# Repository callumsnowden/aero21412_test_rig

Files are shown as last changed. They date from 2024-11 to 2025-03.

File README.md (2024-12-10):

# aero21412_test_rig
AERO21412 Avionics Coursework 1 – Wind Tunnel Test Rig "Black Box"

## Description
A "black box" PCB that provides the interface between a number of sensors on the wind tunnel test rig and an external data acquisition system.The aim is to provide a number of outputs measuring supply voltage and current; motor torque, thrust and rotational speed. A PWM input signal should be provided that is passed directly to the ESC module.

## Signals to/from DAS
- [] RPM as voltage with scaling factor
- [] Scaled supply voltage
- [] Supply current as voltage with scaling factor
- [] UART for force measurements (optional control input)

## UART measurement packet specification

`<AAA,BB.BBB,CC.CCC>`

Measurements are transmitted at 20 Hz. The packet consists of a start character of `<` followed by an incrementing three-digit frame identifier `AAA`. After this follows a three decimal place measurement of thrust in Newtons `BB.BBB` and then a three decimal place measurement of torque in Newton metres `CC.CCC`. An end character `>` terminates the packet.

## Hardware

A Raspberry Pi Pico (RP2040) handles interfacing the load cells and photointerruptor and is responsible for transmitting UART messages plus generating an analogue voltage representing RPM.

### Sensors

- One load cell for thrust measurement (Siemens 7MH5102-1PD00) with a rated load of 5kg
- One load cell (analogue voltage output) for torque measurement (TE Connectivity FC2231-0000-0010-L) with a rated load of 10lbf (13.5 Nm) and a voltage output of 0.5-4.5V
- Photointerruptor for RPM measurement

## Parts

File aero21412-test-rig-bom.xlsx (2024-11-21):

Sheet: Electrical
AERO21412 Test Rig BOM
Rig build qty: | 1
Part | Manufacturer | Manufac. Part No. | Quantity Per Rig | Quantity to order total
1uF 0603 Cap | Samsung Electro-Mechanics | CL10A105KA8NNNC | 8 | 8
0.1uF 0603 Cap | Kemet | C0603C104Z3VAC7411 | 7 | 7
10uF 0603 Cap | Samsung Electro-Mechanics | CL10A106MP8NNNC | 2 | 2
22uF elec. Cap | Kemet | A768EB226M1HLAE048 | 1 | 1
47uF elec. Cap | Kemet | A768EB476M1VLAE042 | 1 | 1
SMAJ5.0A/TR13 | Yageo | SMAJ5.0A/TR13 | 4 | 4
CDSOT23-T05C | Bourns | CDSOT23-T05C | 3 | 3
Green LED | AMS Osram | KT EELP41.12-S2U1-25-2X4X-5-R18 | 1 | 1
4 pin WTB header | Molex | 22-27-2041 | 3 | 3
DB15 female conn. | Multicomp Pro | 5504F1-15S-02-03-F1 | 1 | 1
XT60-M connector | Amass | XT60-M | 1 | 1
XT60-F connector | Amass | XT60-F | 1 | 1
Molex connector | Molex | 22-27-2031 | 1 | 1
1x3 pin header | Multicomp Pro | 2211S-03G | 1 | 1
2x5 pin header | Multicomp Pro | 2213S-10G | 1 | 1
3.3uH ferrite | Wurth Elektronik | 742792656 | 1 | 1
MMBT4403 | Onsemi | MMBT4403LT1G | 1 | 1
2N7002BK,215 | Diodes Inc. | 2N7002BK,215 | 1 | 1
NX3008PBK,215 | Nexperia | NX3008PBK,215 | 1 | 1
100R 0603 resistor | Vishay | RCA0603100RFKEA | 2 | 2
3.3K 0603 resistor | Yageo | RC0603FR-133K3L | 6 | 6
20K 0603 resistor | Yageo | RC0603FR-1320KL | 2 | 2
8.2K 0603 resistor | Yageo | RC0603JR-078K2L | 1 | 1
110R 0805 resistor | Yageo | RC0805FR-07110RL | 1 | 1
1.6K 0603 resistor | Yageo | RC0603FR-071K6L | 1 | 1
5.1K 0603 resistor | Yageo | AC0603FR-135K1L | 1 | 1
9.76K 0603 resistor | Panasonic | ERJ3EKF9761V | 1 | 1
10K 0603 resistor | KOA | RK73B1JTTD103J | 1 | 1
2K 0603 resistor | KOA | RK73H1JTTD2001F | 1 | 1
1K 0603 resistor | KOA | RK73H1JTTD1001F | 4 | 4
Push button | TE Connectivity | FSM4JH | 1 | 1
Microcontroller | Raspberry Pi | RASPBERRY PI PICO | 1 | 1
ADS1100 | Texas Instruments | ADS1100A3IDBVT | 1 | 1
TXU0202DCUR | Texas Instruments | TXU0202DCUR | 1 | 1
LMV321 | Texas Instruments | LMV321IDBVR | 2 | 2
Current sensor | Allegro Microsystems | ACS724LLCTR-50AB-S | 1 | 1
5V PSU | XP Power | TR05S05 | 1 | 1
Photo interruptor | TT Electronics | OPB743WZ | 1 | 1
Strain gauge | Siemens | 7MH5102-1PD00 | 1 | 1
Load cell | TE Connectivity | FC2231-0000-0010-L | 1 | 1

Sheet: Mechanical
AERO21412 Test Rig BOM
Rig build qty: | 1
Part | Manufacturer | Manufac. Part No. | Quantity Per Rig | Quantity to order total
Plain bearing | Igus | GFL-10 | 2 | 2
10mm ID Shaft collar | RS Pro | 823-6954 | 2 | 2

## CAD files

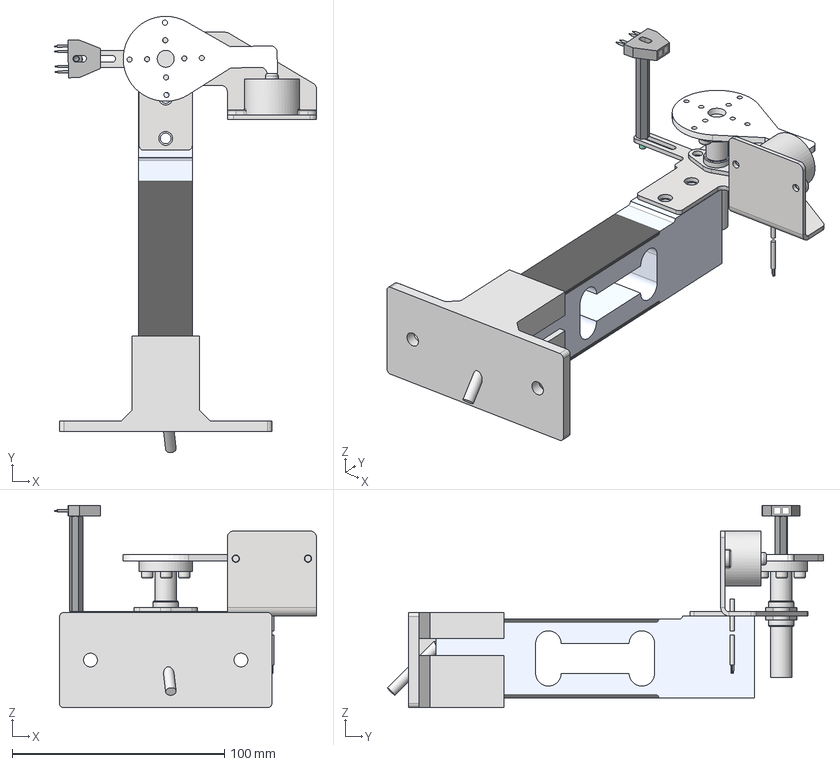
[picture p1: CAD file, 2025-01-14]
mechanical/MainAssembly.stp
123.4 x 205.4 x 95.2 mm
MotorMountPlate
MotorPlateSpindle
TorqueSensorMountPlate
ibh_GFL-10_2024102_1050_model x 2
c-fc2231-0000-0010-l-d-3d
7MH5102-1PD00_G_WT01_XX_00448V
ISO 4762 - M3 x 8 x 4
BaseStand
OPB742WZ
Download_STEP_971450321 (rev1)

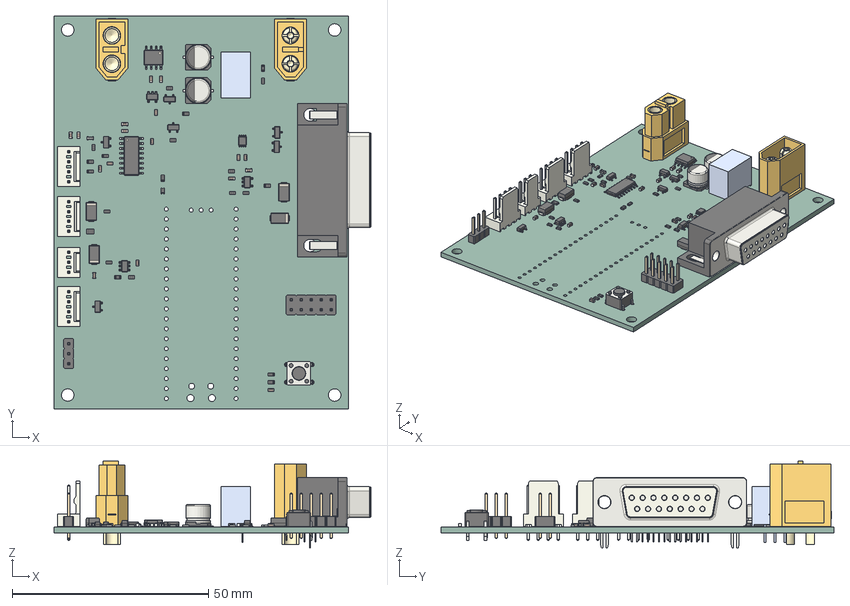
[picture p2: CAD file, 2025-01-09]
test-rig-black-box/test-rig-black-box.step
80.8 x 100.0 x 22.1 mm
SOT_23 x 6
C_0603_1608Metric x 17
R_0603_1608Metric x 20
DSUB_43_female
TR05
D_SMA x 4
VSSOP_8_23x2mm_P05mm
SOIC_8_39x49mm_P127mm
Molex_AE_6410_04A x 3
XT60 male v9
XT60 female v5
PinHeader_2x05_P254mm_Vertical
CP_Elec_63x57 x 2
D_0603
Molex_AE_6410_03A
R_0805_2012Metric
L_0603_1608Metric
SOT_23_5 x 2
SOT_23_6
SW_PUSH_6mm
SOP-16_3.9x9.9mm_P1.27mm
PinHeader_1x03_P254mm_Vertical
test-rig-black-box_PCB

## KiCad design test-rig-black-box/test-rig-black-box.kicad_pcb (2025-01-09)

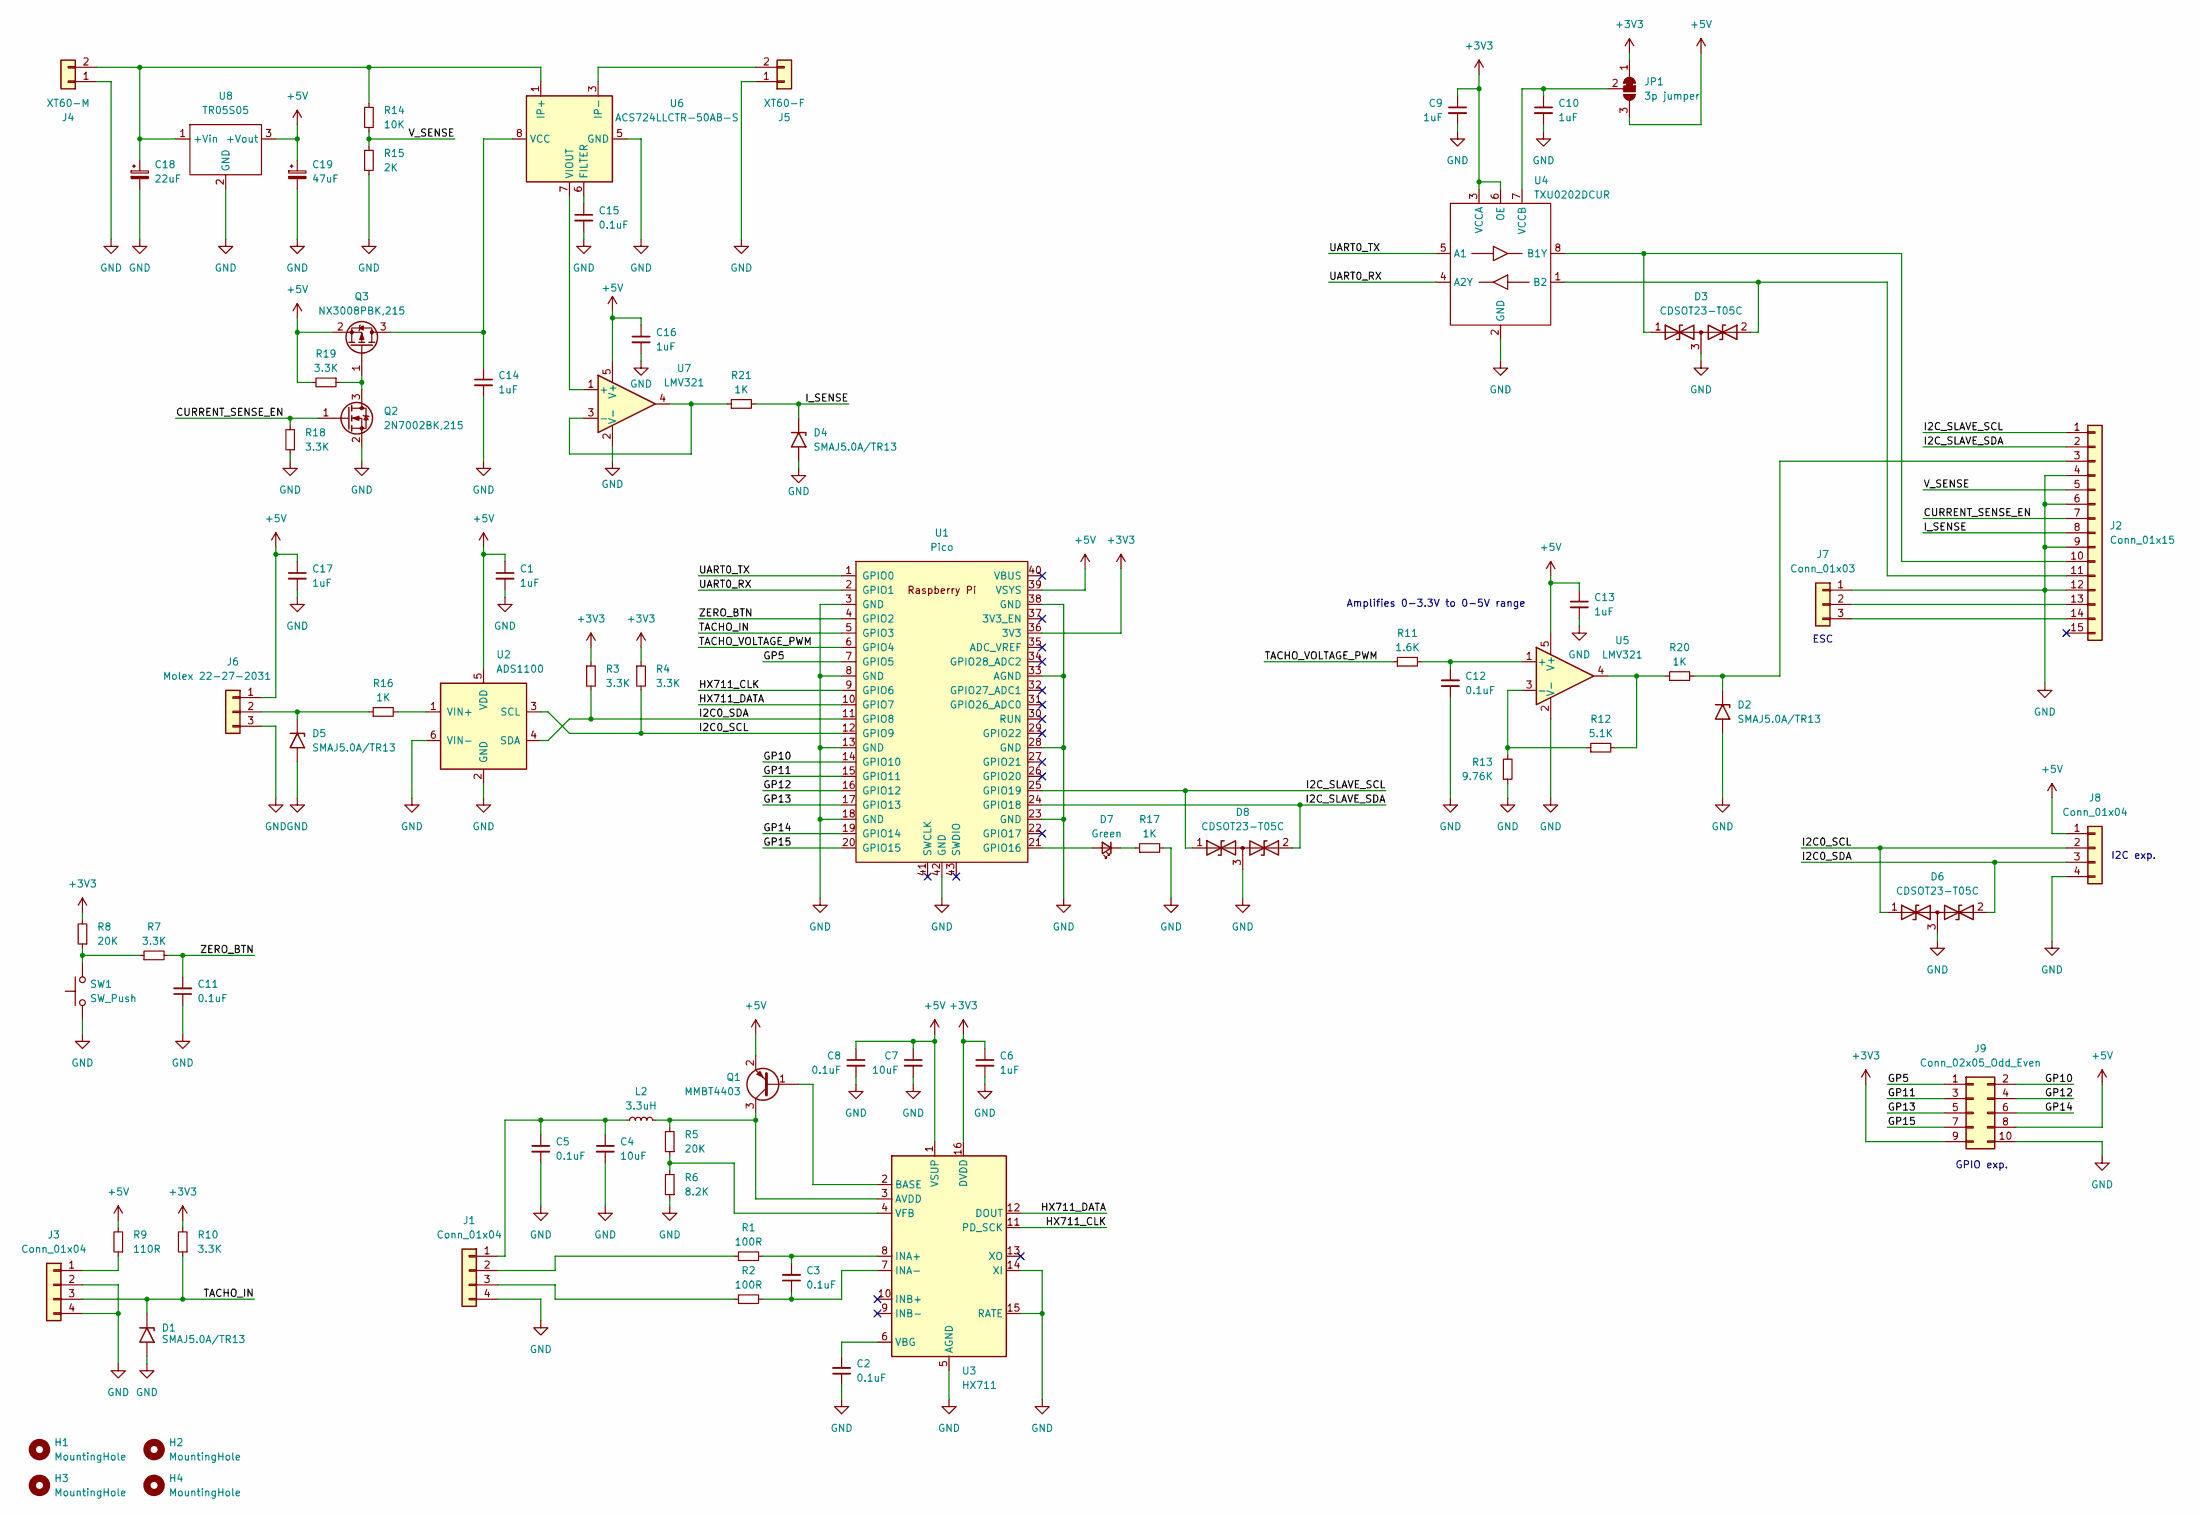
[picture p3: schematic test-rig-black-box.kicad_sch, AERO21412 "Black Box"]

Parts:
C1, C6, C9, C10, C13, C14, C16, C17: 1uF; C_0603_1608Metric; ManufacturerPartNumber CL10A105KA8NNNC
C2, C3, C5, C8, C11, C12, C15: 0.1uF; C_0603_1608Metric; ManufacturerPartNumber C0603C104Z3VAC7411
C4, C7: 10uF; C_0603_1608Metric; ManufacturerPartNumber CL10A106MP8NNNC
C18: 22uF; CP_Elec_6.3x5.7; ManufacturerPartNumber A768EB226M1HLAE048
C19: 47uF; CP_Elec_6.3x5.7; ManufacturerPartNumber A768EB476M1VLAE042
D1, D2, D4, D5: SMAJ5.0A/TR13; D_SMA; ManufacturerPartNumber SMAJ5.0A/TR13
D3, D6, D8: CDSOT23-T05C; SOT-23; ManufacturerPartNumber CDSOT23-T05C
D7: Green; D_0603_1608Metric; ManufacturerPartNumber KT EELP41.12-S2U1-25-2X4X-5-R18
H1, H2, H3, H4: MountingHole; MountingHole_3.2mm_M3
J1, J3, J8: Conn_01x04; Molex_KK-254_AE-6410-04A_1x04_P2.54mm_Vertical; ManufacturerPartNumber 22-27-2041
J2: Conn_01x15; DSUB-15_Female_Horizontal_P2.77x2.84mm_EdgePinOffset7.70mm_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; ManufacturerPartNumber 5504F1-15S-02-03-F1
J4: XT60-M; AMASS_XT60-M_1x02_P7.20mm_Vertical; ManufacturerPartNumber XT60-M
J5: XT60-F; AMASS_XT60-F_1x02_P7.20mm_Vertical; ManufacturerPartNumber XT60-F
J6: Molex 22-27-2031; Molex_KK-254_AE-6410-03A_1x03_P2.54mm_Vertical; ManufacturerPartNumber 22-27-2031
J7: Conn_01x03; PinHeader_1x03_P2.54mm_Vertical; ManufacturerPartNumber 2211S-03G
J9: Conn_02x05_Odd_Even; PinHeader_2x05_P2.54mm_Vertical; ManufacturerPartNumber 2213S-10G
JP1: 3p jumper; SolderJumper-3_P1.3mm_Bridged12_RoundedPad1.0x1.5mm_NumberL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
L2: 3.3uH; L_0603_1608Metric; ManufacturerPartNumber 742792656
Q1: MMBT4403; SOT-23; ManufacturerPartNumber MMBT4403LT1G
Q2: 2N7002BK,215; SOT-23; ManufacturerPartNumber 2N7002BK,215
Q3: NX3008PBK,215; SOT-23; ManufacturerPartNumber NX3008PBK,215
R1, R2: 100R; R_0603_1608Metric; ManufacturerPartNumber RCA0603100RFKEA
R3, R4, R7, R10, R18, R19: 3.3K; R_0603_1608Metric; ManufacturerPartNumber RC0603FR-133K3L
R5, R8: 20K; R_0603_1608Metric; ManufacturerPartNumber RC0603FR-1320KL
R6: 8.2K; R_0603_1608Metric; ManufacturerPartNumber RC0603JR-078K2L
R9: 110R; R_0805_2012Metric; ManufacturerPartNumber RC0805FR-07110RL
R11: 1.6K; R_0603_1608Metric; ManufacturerPartNumber RC0603FR-071K6L
R12: 5.1K; R_0603_1608Metric; ManufacturerPartNumber AC0603FR-135K1L
R13: 9.76K; R_0603_1608Metric; ManufacturerPartNumber ERJ3EKF9761V
R14: 10K; R_0603_1608Metric; ManufacturerPartNumber RK73B1JTTD103J
R15: 2K; R_0603_1608Metric; ManufacturerPartNumber RK73H1JTTD2001F
R16, R17, R20, R21: 1K; R_0603_1608Metric; ManufacturerPartNumber RK73H1JTTD1001F
SW1: SW_Push; SW_PUSH_6mm; ManufacturerPartNumber FSM4JH
U1: Pico; RPi_Pico_SMD_TH; ManufacturerPartNumber Pico
U2: ADS1100; SOT-23-6; ManufacturerPartNumber ADS1100A3IDBVT
U3: HX711; SOP-16_3.9x9.9mm_P1.27mm; ManufacturerPartNumber HX711
U4: TXU0202DCUR; VSSOP-8_2.3x2mm_P0.5mm; ManufacturerPartNumber TXU0202DCUR
U5, U7: LMV321; SOT-23-5; ManufacturerPartNumber LMV321IDBVR
U6: ACS724LLCTR-50AB-S; SOIC-8_3.9x4.9mm_P1.27mm; ManufacturerPartNumber ACS724LLCTR-50AB-S
U8: TR05S05; TR05Sxx; ManufacturerPartNumber TR05S05

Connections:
+3V3: C6.1, C9.1, J9.9, JP1.1 (A), R3.1, R4.1, R8.2, R10.2, U1.36 (3V3), U3.16 (DVDD), U4.3 (VCCA), U4.6 (OE)
+5V: C1.1, C7.1, C8.1, C13.1, C16.1, C17.1, C19.1, J6.1, J8.1, J9.8, JP1.3 (B), Q1.2 (E), Q3.2 (S), R9.2, R19.2, U1.39 (VSYS), U2.5 (VDD), U3.1 (VSUP), U5.5 (V+), U7.5 (V+), U8.3 (+Vout)
/CURRENT_SENSE_EN: J2.7, Q2.1 (G), R18.2
/GP5: J9.1, U1.7 (GPIO5)
/GP10: J9.2, U1.14 (GPIO10)
/GP11: J9.3, U1.15 (GPIO11)
/GP12: J9.4, U1.16 (GPIO12)
/GP13: J9.5, U1.17 (GPIO13)
/GP14: J9.6, U1.19 (GPIO14)
/GP15: J9.7, U1.20 (GPIO15)
/HX711_CLK: U1.9 (GPIO6), U3.11 (PD_SCK)
/HX711_DATA: U1.10 (GPIO7), U3.12 (DOUT)
/I2C0_SCL: D6.1 (A1), J8.2, R4.2, U1.12 (GPIO9), U2.3 (SCL)
/I2C0_SDA: D6.2 (A2), J8.3, R3.2, U1.11 (GPIO8), U2.4 (SDA)
/I2C_SLAVE_SCL: D8.1 (A1), J2.1, U1.25 (GPIO19)
/I2C_SLAVE_SDA: D8.2 (A2), J2.2, U1.24 (GPIO18)
/I_SENSE: D4.1 (A1), J2.8, R21.2
/TACHO_IN: D1.1 (A1), J3.3, R10.1, U1.5 (GPIO3)
/TACHO_VOLTAGE_PWM: R11.1, U1.6 (GPIO4)
/UART0_RX: U1.2 (GPIO1), U4.4 (A2Y)
/UART0_TX: U1.1 (GPIO0), U4.5 (A1)
/V_SENSE: J2.5, R14.2, R15.1
/ZERO_BTN: C11.2, R7.2, U1.4 (GPIO2)
GND: C1.2, C2.1, C4.2, C5.2, C6.2, C7.2, C8.2, C9.2, C10.2, C11.1, C12.1, C13.2, C14.2, C15.2, C16.2, C17.2, C18.2, C19.2, D1.2 (A2), D2.2 (A2), D3.3 (common), D4.2 (A2), D5.2 (A2), D6.3 (common), D8.3 (common), J1.4, J2.4, J2.6, J2.9, J2.12, J3.2, J3.4, J4.1, J5.1, J6.3, J7.1, J8.4, J9.10, Q2.2 (S), R6.1, R13.1, R15.2, R17.2, R18.1, SW1.1, U1.3 (GND), U1.8 (GND), U1.13 (GND), U1.18 (GND), U1.23 (GND), U1.28 (GND), U1.33 (AGND), U1.38 (GND), U1.42 (GND), U2.2 (GND), U2.6 (VIN-), U3.5 (AGND), U3.14 (XI), U3.15 (RATE), U4.2 (GND), U5.2 (V-), U6.5 (GND), U7.2 (V-), U8.2 (GND)
unnamed: D2.1 (A1), J2.3, R20.2
unnamed: D3.1 (A1), J2.10, U4.8 (B1Y)
unnamed: D3.2 (A2), J2.11, U4.1 (B2)
unnamed: D5.1 (A1), J6.2, R16.1
unnamed: D7.2 (A), U1.21 (GPIO16)
unnamed: D7.1 (K), R17.1
unnamed: C4.1, C5.1, J1.1, L2.1
unnamed: J1.2, R1.1
unnamed: J1.3, R2.1
unnamed: J2.13, J7.2
unnamed: J2.14, J7.3
unnamed: J3.1, R9.1
unnamed: C18.1, J4.2, R14.1, U6.1 (IP+), U6.2 (IP+), U8.1 (+Vin)
unnamed: J5.2, U6.3 (IP-), U6.4 (IP-)
unnamed: C10.1, JP1.2 (C), U4.7 (VCCB)
unnamed: Q1.1 (B), U3.2 (BASE)
unnamed: L2.2, Q1.3 (C), R5.2, U3.3 (AVDD)
unnamed: Q2.3 (D), Q3.1 (G), R19.1
unnamed: C14.1, Q3.3 (D), U6.8 (VCC)
unnamed: R7.1, R8.1, SW1.2
unnamed: R12.2, R20.1, U5.4
unnamed: R16.2, U2.1 (VIN+)
unnamed: C3.2, R1.2, U3.8 (INA+)
unnamed: C3.1, R2.2, U3.7 (INA-)
unnamed: C2.2, U3.6 (VBG)
unnamed: R5.1, R6.2, U3.4 (VFB)
unnamed: C12.2, R11.2, U5.1 (+)
unnamed: R12.1, R13.2, U5.3 (-)
unnamed: C15.1, U6.6 (FILTER)
unnamed: U6.7 (VIOUT), U7.1 (+)
unnamed: R21.1, U7.3 (-), U7.4

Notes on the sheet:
GPIO exp.
Amplifies 0-3.3V to 0-5V range
ESC
I2C exp.

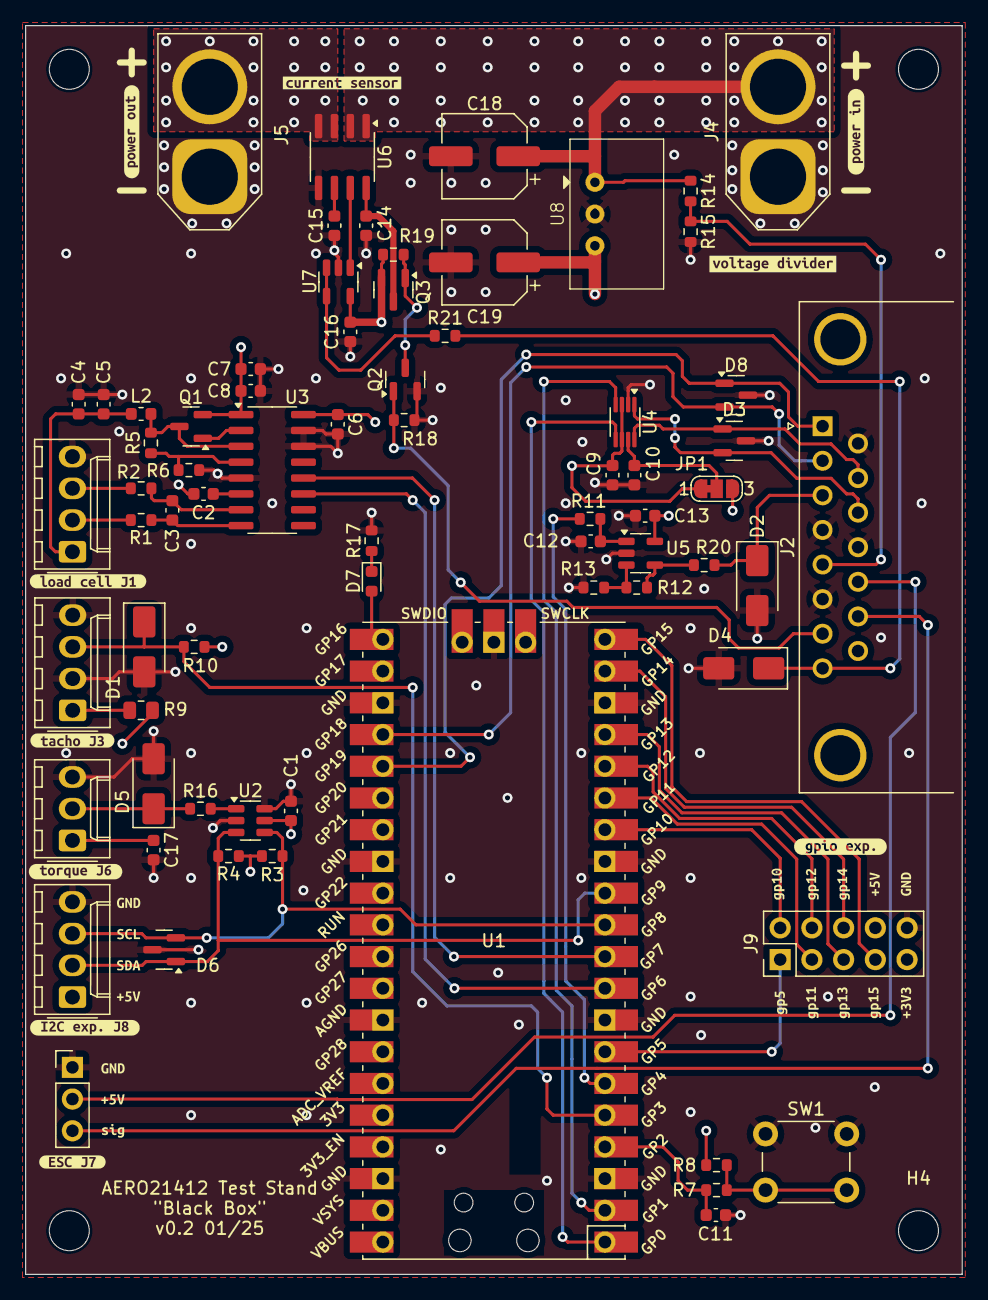
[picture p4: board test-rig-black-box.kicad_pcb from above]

Board: 4 copper layers, 75.0 x 100.0 mm, 102 parts (0 on the bottom side), 55 nets.

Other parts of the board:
kibuzzard-672A2B3E: G***; kibuzzard-672A2B3E
kibuzzard-672A2B23: G***; kibuzzard-672A2B23
kibuzzard-671770C0: G***; kibuzzard-671770C0
kibuzzard-671770F1: G***; kibuzzard-671770F1
kibuzzard-671770F6: G***; kibuzzard-671770F6
kibuzzard-671771D1, kibuzzard-671771D1#2: G***; kibuzzard-671771D1
kibuzzard-671771D9, kibuzzard-671771D9#2: G***; kibuzzard-671771D9
kibuzzard-671771E1: G***; kibuzzard-671771E1
kibuzzard-671772CC: G***; kibuzzard-671772CC
kibuzzard-671772D6: G***; kibuzzard-671772D6
kibuzzard-671773D8: G***; kibuzzard-671773D8
kibuzzard-671775A0: G***; kibuzzard-671775A0
kibuzzard-6717711C: G***; kibuzzard-6717711C
kibuzzard-6717717D: G***; kibuzzard-6717717D
kibuzzard-6717758B: G***; kibuzzard-6717758B
kibuzzard-67177092: G***; kibuzzard-67177092
kibuzzard-67177102: G***; kibuzzard-67177102
kibuzzard-67177109: G***; kibuzzard-67177109
kibuzzard-67177114: G***; kibuzzard-67177114
kibuzzard-67177127: G***; kibuzzard-67177127
kibuzzard-67177131: G***; kibuzzard-67177131
kibuzzard-67177240: G***; kibuzzard-67177240
kibuzzard-67177262: G***; kibuzzard-67177262
kibuzzard-67177297: G***; kibuzzard-67177297
kibuzzard-67177472: G***; kibuzzard-67177472

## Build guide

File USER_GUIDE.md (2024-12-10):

# Black Box User's Manual

## Theory of Operation
The "black box" takes a number of sensor inputs, performs processing and then outputs a range of analogue outputs suitable for connecting to a data acquisition system (DAS).

A load cell measuring torque is connected to an ADS1100 I2C analogue-to-digital converter interfaced with the Raspberry Pi Pico which then scales the reading to a 0-2.2Nm torque value.

A load cell measuring thrust is connected to a HX711 wheatstone bridge amplifier again interfaced with the Raspberry Pi Pico. The reading is scaled to 0-49N thrust value.

Revolutions per minute are sensed by a photoreflective sensor, with an analogue voltage then produced by the Raspberry Pi Pico that corresponds 0-5V at 0-10,000RPM.

Torque & thrust measurements along with a frame counter are emitted at 20Hz over a 3.3V UART connection to the DAS.

## System block diagram

Block diagram of system functional components

## Board connection
1. Attach motor to front of torque measurement arm using appropriate mounting hardware (NOTE: the mounting holes are tapped to accept M3 mounting hardware)
2. Attach propellor under test to the motor using appropriate mounting hardware
3. Connect ESC motor wires to motor
4. Connect the ESC to XT60 female connector J5 (marked "POWER OUT")
5. Connect the thrust load cell (4-pin Molex KK connector) to J1 (marked "LOAD CELL")
6. Connect the torque load cell (3-pin Molex KK connector) to J6 (marked "TORQUE")
7. Connect the photoreflective sensor (4-pin Molex KK connector) to J3 (marked "TACHO")
8. Plug the DAS breakout cable (male DB-15 connector) into J2
9. Wire the DAS as required
10. Connect power to XT60 male connector J4 (marked "POWER IN")

## Board initialisation
Once the board is suitably wired and power applied, a zeroing cycle needs to be performed.

- Zero status is indicated by the green LED marked D7. When not illuminated, zeroing needs to be perfomed (see below)

Zeroing mostly applies the the load cell used to measure torque as due to environmental changes and sensor noise the zero point can drift slightly. It also serves to set the correct offset for the thrust load cell, accounting for any mass present.

To zero the system, press button "SW1" located in the south-east corner of the board.

The zero cycle takes around one second to complete, where a number of sensor readings are taken, averaged and then offsets applied as necessary. Once the cycle has complete, the green LED D7 should illuminate.

During operation (i.e. with an experimental cycle being run) the LED should remain illuminated. Upon returning to zero throttle the LED may begin to blink - this is the board running an automatic zeroing procedure as the zero may have drifted (equivalent to pressing the button). __Wait to run the next experimental cycle until the LED remains steadily lit!__

During zeroing, the UART output will pause (the frame counter will not increment during this time) as the firmware waits in a loop to average sensor readings. Once complete, the output will resume.

## Debug data
The USB port located on the Raspberry Pi Pico exposes a serial port when plugged into a computer. This outputs a line format that contains the raw counts from the ADC, HX711, torque force, calculated torque and thrust and the calculated photoreflector frequency (times this value by 60 to get motor RPM). An additional "CAL" status is present, this reflects whether the board has had first zeroing performed.

An example of the line format is `ADCV 0.513V, HX711 -206, TQF -0.00N, TQ -0.000Nm, THR 0.000N, TACHO 0.0Hz, CAL True`

## Firmware explanation
Firmware for the black box is written in MicroPython to lower the barrier to entry for modifications and understanding of the code.

The firmware has one external dependency on the `hx711-pico-mpy` library sourced from [here](https://github.com/endail/hx711-pico-mpy).

Hardware utilised by the firmware include the I2C, PWM, UART, timer and PIO peripherals.

A timer running at 20Hz fires an interrupt that calls `uart_timer_callback`. This is the function that increments the frame counter and emits a data frame over the UART.

A pin interrupt watches for a falling edge on the photoreflector tachometer input, calculates a difference in microseconds between interrupts and then a frequency which directly corresponds to the motor RPM.

A `while True` loop forms the main program loop. This repeatedly reads  both the ADC & HX711, performs smoothing on both (in the case of the HX711 a simple moving average is taken which slows the load cell response) and then calculates torque and thrust.

A scaling is applied to the tacho frequency value that scales from zero to the upper frequency limit (calculated in the code) to arbitrary PWM units and then outputs this value for low-pass filtering.

An `if` statement performs automatic zeroing by watching for a negative torque value and then calling the `zero_sensors` function.

Another `if` statement performs automatic zeroing by watching for the raw reading from the HX711 wandering outside a specified window. Sometimes this can occur if the torque sensor is calibrated and the HX711 returns a bogus value at the same time.

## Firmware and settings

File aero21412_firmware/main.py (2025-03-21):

import math
from machine import Pin, I2C, PWM, UART, Timer
from time import ticks_us, sleep
from src.hx711 import *

'''
AERO21412 "Black Box" MicroPython firmware
v0.1 12/2024

Dependencies:
hx711-pico-mpy https://github.com/endail/hx711-pico-mpy
    - Copy entire "src" folder to the Pico, then delete "__init.py__"
'''

# Functions
def calculate_moving_average(new_data_point, data_list, average_size):
    # Add fresh data
    data_list.insert(0, new_data_point)
    try:
        # Remove nth item in list
        data_list.pop(average_size)
    except Exception as e:
        pass
    total = 0
    total = sum(data_list)
        
    value = math.ceil(total / len(data_list))
    if(value == None):
        return 0
    else:
        return value

def calc_time(p):
    global last_tacho_time, tacho_freq
    entry_ticks_us = ticks_us()
    time_delta = entry_ticks_us - last_tacho_time
    tacho_freq = float(1.0 / (time_delta / 1000000))
    last_tacho_time = entry_ticks_us
    
def zero_sensors(p, hx711_handle):
    global thrust_zero_value, torque_zero_value, LED_STATE
    torque_avg = []
    thrust_avg = 0
    thrust_averaging_window = 10
    thrust_raw_values = []
    
    # Take an average of readings
    for x in range(0, 10):
        hx_val = hx711_handle.get_value()
        thrust_avg = calculate_moving_average(hx_val, thrust_raw_values, thrust_averaging_window)
        
        raw_adc_data = i2c.readfrom(ads1100_addr, 3)
        adc_voltage = (5.0/16384) * ((raw_adc_data[0] << 8) | raw_adc_data[1])
        torque_avg.append(adc_voltage)
        
        sleep(0.05)
    
    torque_zero_value = sum(torque_avg) / len(torque_avg)
    thrust_zero_value = thrust_avg
    LED_STATE = True
    
def num_to_range(num, inMin, inMax, outMin, outMax):
    return outMin + (float(num - inMin) / float(inMax - inMin) * (outMax
        - outMin))

def uart_timer_callback(t):
    global frame_id, thrust, torque
    if frame_id == 1000:
        frame_id = 0
        
    # Emit packet over UART
    data_uart.write("<{0:03},{1:0>2.3f},{2:0>2.3f}>".format(frame_id, thrust, torque))
    frame_id = frame_id + 1

# GPIO configuration
scl_pin = Pin(9)
sda_pin = Pin(8)
hx_clk_pin = Pin(6)
hx_data_pin = Pin(7)
led_pin = Pin(16, mode=Pin.OUT)
button_pin = Pin(2, mode=Pin.IN)
tacho_in_pin = Pin(3, mode=Pin.IN)
tacho_pwm_pin = Pin(4)
uart_tx = Pin(0)
uart_rx = Pin(1)

tacho_in_pin.irq(handler=calc_time, trigger=Pin.IRQ_FALLING)

tacho_pwm = PWM(tacho_pwm_pin, freq=100000, duty_u16=0) # Init PWM at 100kHz, no duty to start
data_uart = UART(0, baudrate=115200, tx=uart_tx, rx=uart_rx)

# ADS1100 configuration
ads1100_addr = 0x4B
ads1100_conf = 0x08

# Misc. variables
adc_vcc_const = 4.85 # 5V voltage, measured on board
last_tacho_time = 0 # Used for interrupt timing
tacho_freq = 0.0 # Calculated frequency based on interrupt timing
torque_zero_value = 0 # Stored when zero button is pressed
thrust_zero_value = 0 # Stored when zero button is pressed
raw_adc_data = [] # Buffer for data from I2C ADC
max_rpm = 25000 # Maximum expected input RPM
max_frequency = (max_rpm / 60) # Calculated, used as top of map value for PWM output
torque_arm_length = 50 # Length from motor centre point to load cell, in mm

# Final variables sent over UART
thrust = 0
torque = 0
frame_id = 0

LED_STATE = False

global hx
# Configure HX711 (clock 6, data 7)
hx = hx711(hx_clk_pin, hx_data_pin)
hx.set_power(hx711.power.pwr_up)
hx.set_gain(hx711.gain.gain_128)
hx.set_power(hx711.power.pwr_down)
hx.wait_power_down()
hx.set_power(hx711.power.pwr_up)
hx.wait_settle(hx711.rate.rate_80)

# Configure I2C
i2c = I2C(0, scl=scl_pin, sda=sda_pin, freq=100000)

# Configure ADC for 16sps, 1x PGA
i2c.writeto(ads1100_addr, int.to_bytes(ads1100_conf))

def main():
    global adc_voltage, hx_val, torque_zero_value, thrust_zero_value, LED_STATE, thrust, torque, frame_id
    
    thrust_raw_values = []
    thrust_averaging_window = 15
    
    '''
    Important to update this per board!
    1. Monitor the USB UART debug output
    2. Zero the scale (some zero point variation is expected, can be safely ignored assuming a range of +/- 100 counts)
    3. Add a known mass and then take note of the "HX711" value on the debug output
    4. Calculate const = loaded count / mass (N)
    '''
    thrust_scale_const = 86006.493
    
    # Establish a timer to ensure 20Hz UART data rate
    uart_timer = Timer(period=50, mode=Timer.PERIODIC, callback=uart_timer_callback)
    
    while True:
        if button_pin.value() == 0:
            zero_sensors(None, hx)
            hx_val = calculate_moving_average(hx.get_value(), thrust_raw_values, thrust_averaging_window)
            hx_val = hx_val - thrust_zero_value
            
            if hx_val < -50 or hx_val > 50:
                # Re-run calibration, occasionally the HX711 cal gets screwy
                zero_sensors(None, hx)

        # Read HX711 value
        hx_val = calculate_moving_average(hx.get_value(), thrust_raw_values, thrust_averaging_window)
        hx_val = hx_val - thrust_zero_value
        
        # Calculate force on thrust load cell
        thrust = abs(round(hx_val / thrust_scale_const, 3))
        
        # Convert ADC reading into voltage - ignore any negative swing in the readings (ADC is pseudo-differential)
        raw_adc_data = i2c.readfrom(ads1100_addr, 3)
        adc_voltage = round((5.0/16384) * ((raw_adc_data[0] << 8) | raw_adc_data[1]), 3)
        
        # Map ADC voltage directly to a force in N (44.39N value is calculated from 4.53kgf * 9.8 where 4.53 is the maximum the load cell can measure)
        torque_force = round(num_to_range(adc_voltage, torque_zero_value, 4.50, 0, 44.39), 2)
        
        # If we have a negative torque value then calibrate - load cell has been unloaded and zero point has drifted slightly
        if torque_force < 0:
            torque_force = 0
            LED_STATE = False
            led_pin.value(LED_STATE)
            zero_sensors(None, hx)
        
        # Calculate actual torque from arm length and measured force
        torque = torque_force * (torque_arm_length / 1000)
        
        # Scale tacho frequency to PWM range and update
        tacho_pwm.duty_u16(int(num_to_range(tacho_freq, 0, max_frequency, 0, 65535)))

        # Quickly calculate RPM for debugging purposes
        motor_rpm = tacho_freq * 60
        
        # Debug printing to USB serial interface
        print("ADCV {}V, HX711 {}, TQF {:0>2.2f}N, TQ {:0>2.3f}Nm, THR {:0>2.3f}N, TACHO {:0>2.1f} RPM, CAL {}".format(adc_voltage, hx_val, torque_force, torque, thrust, motor_rpm, LED_STATE))
        
        led_pin.value(LED_STATE)

if __name__ == "__main__":
    main()

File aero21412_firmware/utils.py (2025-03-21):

import math
from machine import Pin, PWM

'''
AERO21412 utility & test functions
'''

max_rpm = 25000 # Used for scaling function
max_frequency = (max_rpm / 60) # Calculated, used as top of map value for PWM output

# Pins
tacho_pwm_pin = Pin(4)
led_pin = Pin(16, mode=Pin.OUT)
button_pin = Pin(2, mode=Pin.IN)
tacho_pwm = PWM(tacho_pwm_pin, freq=100000, duty_u16=0) # Init PWM at 100kHz, no duty to start

def num_to_range(num, inMin, inMax, outMin, outMax):
    return outMin + (float(num - inMin) / float(inMax - inMin) * (outMax
        - outMin))

def ledon():
	led_pin.value(1)

def ledoff():
	led_pin.value(0)

def emitspeed(rpm):
	tacho_freq = rpm / 60
	tacho_pwm.duty_u16(int(num_to_range(tacho_freq, 0, max_frequency, 0, 65535)))

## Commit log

2024-10-18 Start work on PCB layout
    [test-rig-black-box.kicad_pcb, test-rig-black-box.kicad_sch]
2024-11-21 v0.1 PCB design
    - Added gerbers
    - BOM generated
    [aero21412-test-rig-bom.xlsx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]
2024-12-03 Fix orientation of TVS diodes
    [test-rig-black-box-B_Cu.gbl, test-rig-black-box-B_Mask.gbs, test-rig-black-box-B_Silkscreen.gbo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]
2025-01-09 Update board to v0.2
    - Fix issue with regulator footprint being wrong
    - Fix issue with TVS diodes being the wrong way around
    - Added soldermask over jumper for selecting 3V3/5V UART
    [test-rig-black-box-B_Cu.gbl, test-rig-black-box-B_Mask.gbs, test-rig-black-box-B_Silkscreen.gbo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]
2025-01-14 Create MainAssembly.stp
    Added STEP file for test rig assembly.
    [MainAssembly.stp]
2025-03-21 Minor code updates
    - Add utility functions for board test
    - Change debug serial output to RPM rather than frequency
    - Update maximum motor speed
    - Add note about copying over the hx711-pico-mpy source
    [db15_pin_map.xlsx]
